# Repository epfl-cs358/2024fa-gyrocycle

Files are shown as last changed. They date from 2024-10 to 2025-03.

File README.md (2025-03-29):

# GyroCycle

Welcome to the GyroCycle project's repo!

GyroCycle is a project of building a self-balancing bicycle as part of the [CS-358 course at EPFL](https://edu.epfl.ch/coursebook/en/making-intelligent-things-a-CS-358-A).

This is the result we came up with:

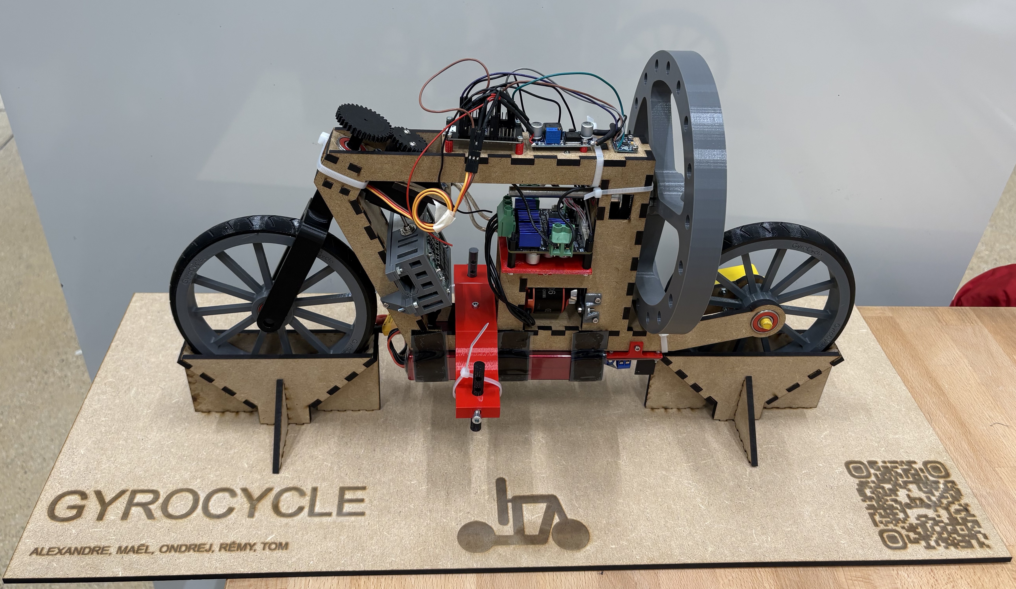
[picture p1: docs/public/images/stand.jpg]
The result bicycle on its stand.


We documented our results along with how to reproduce the build on our [documentation website](https://epfl-cs358.github.io/2024fa-gyrocycle/).

Happy building !

The GyroCycle team.

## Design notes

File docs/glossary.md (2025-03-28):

---
prev: false
next: false
---

<script setup>
    import StlViewer from "./.vitepress/theme/components/StlViewer.vue";
</script>

# Glossary

Some particular words are used for specific meanings in the context of GyroCycle. Those meanings are described here.

## Child Wheels

In the context of GyroCycle, _child wheels_ refer to the safety part of the bike that prevents the bicycle from completely falling on its side. Instead, it stops the fall at a reasonable angle, hence its name.

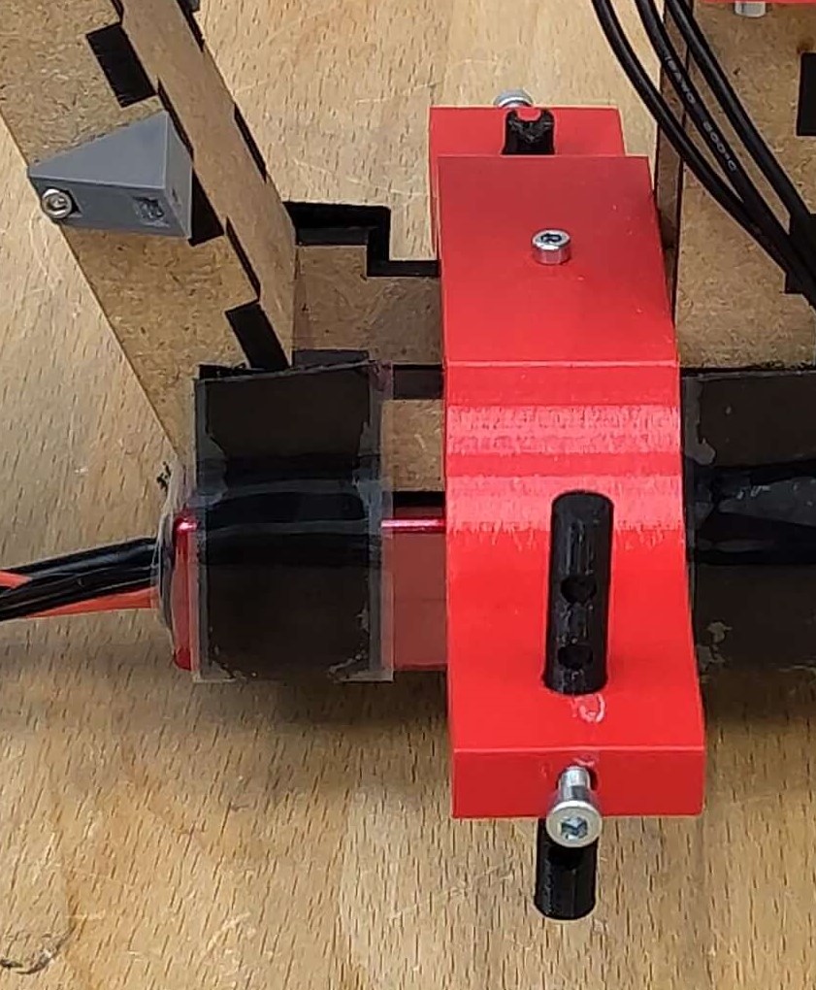
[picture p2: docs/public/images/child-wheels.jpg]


## Flywheel

GyroCycle uses a _flywheel_ to balance. A flywheel is a wheel that rotates to resist changes in motion and counter some other force, in our case the tilt of the bicycle.

When we say flywheel we refer to the big flywheel component at the back of the bicycle.

<StlViewer stlUrl="/2024fa-gyrocycle/stl/to-be-printed/flywheel.stl" />

## Stand

In the context of GyroCycle, the stand is the support structure we built to hold the bicycle upright when it is not balancing, allowing us to showcase it.



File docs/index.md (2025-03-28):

---
title: GyroCycle Docs
prev: false
next: false
---

# GyroCycle

Welcome to our documentation website!

GyroCycle is a course project worked on as part of the [CS-358 course at EPFL](https://edu.epfl.ch/coursebook/en/making-intelligent-things-a-CS-358-A) by a group of five students.

This is the end product:

GyroCycle bicycle on its stand

## Features

The bicycle is designed to balance itself, meaning that when started, it will measure its tilt angle, and rotate the gray flywheel accordingly to compensate for the tilt and stay upright.

One can also connect to the bicycle from a mobile phone using [RemoteXY](https://remotexy.com/en/download/). This way, one can tell the bicycle to steer right and left, and to drive forward and backward.

## Try it

We provide detailed instructions and documents to build your own GyroCycle. See the [guide](./guide/) for more information.

## Video

Here you can see the bike in action (with the noise it makes...).

<video controls="controls" src="/videos/balancing-bicycle.mp4" style="max-height: 50vh;" />

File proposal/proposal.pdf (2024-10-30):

MiT Team Project - GyroCycle | 1

# GyroCycle – Self-balancing bicycle

CS-358 MAKING INTELLIGENT THINGS – TEAM PROJECT PROPOSAL

By Tom Vrakking, Ondrej Zedka, Rémy Berguerand, Maël Imhof and Alexandre Hetet

## Description

Main idea. Create a small scale bicycle that balances itself automatically using physics laws. The bicycle could stay balanced while idle (sationnary) and while moving (forward, backward, turning left or right).
Furthermore, the bicycle could be controlled through a software interface such as a web or mobile app, to make the project more interactive.

Extended idea. Once the main idea is implemented, computer vision could be introduced for the bicycle to drive itself given some instructions or goal.

The motivation behind this project is to play with the laws of physics and build something cool and fun that can be used as a demo for future EPFL students, physics students, …

## Milestone 1 - Gyroscopic Balancing

The first stage focuses on the ability for the bike to balance on its own while stationary or while moving/turning. The stage is divided in three sub-stages

1. Balance when stationary
2. Make the bicycle able to move (forward, backward, turn left and right)
3. Balance while moving

## Stationary balancing

The team will first focus on building the bicycle itself and making sure it is able to automatically balance while stationary.
An accelerometer and gyroscope will be used to measure the bike’s tilt. The microcontroller will then adjust by accelerating the flywheel in the right direction to correct any imbalances.
Field-Oriented Control (FOC) will be used to control the wheel’s motor with the required precision. In addition to the main microcontroller, a FOC driver will thus be needed.
At this stage, the bicycle should already be designed in such a way that adding components for computer vision later does not require a complete redesign.

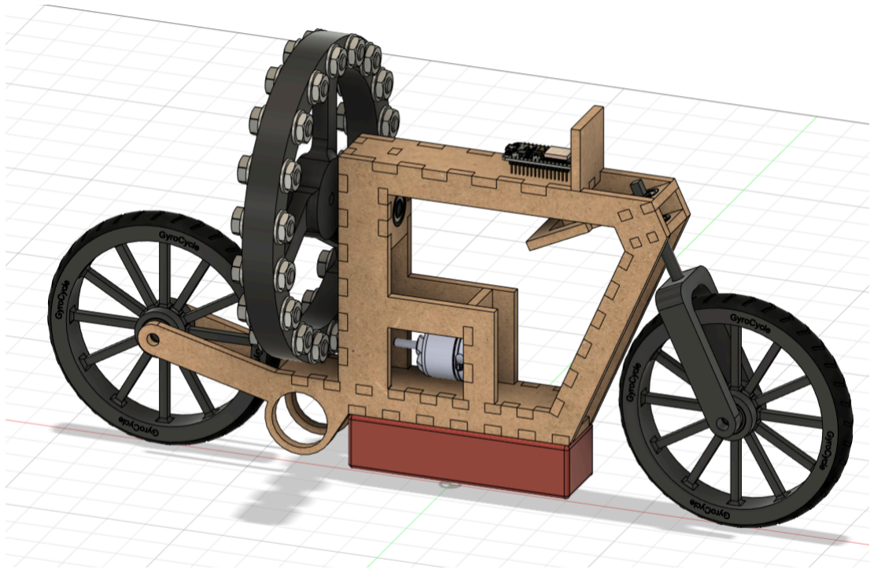
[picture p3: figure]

Mechanical build for stationary balancing. Note that motors for propulsion or steering are not in there yet.

Hardware
- Design and build the bike with computer vision in mind already
- Assemble and mount the electronics
- Make the bike look as pretty as possible
Software
- Implement stationary balancing

## Moving bicycle

Once the bicycle is able to stay balanced while stationary, the team will move on to making it able to move while still balancing itself.
This will require an additional motor for propulsion along with a servo motor for turning left and right.
The software will need to be updated to account for possible movement of the bicycle and to know how to balance it while either stationary or moving.

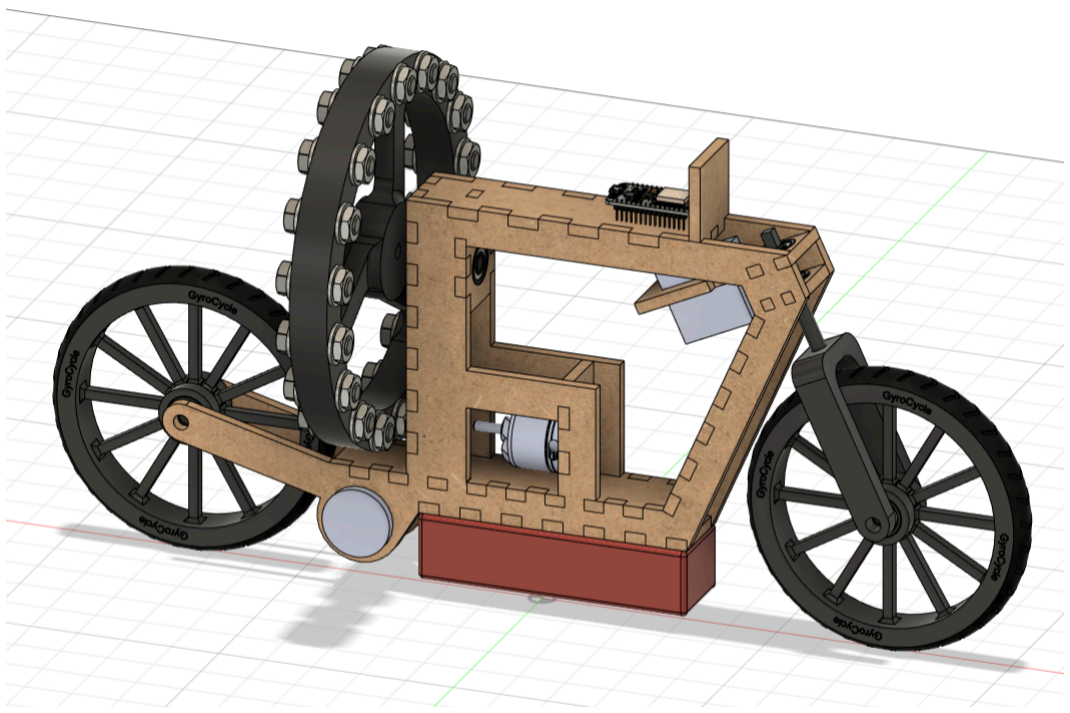
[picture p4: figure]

Moving bike. A propulsion motor is added at the bottom of the flying wheel and a steering servo is added on the front wheel’s axis.

Hardware
- Mount the propulsion motor and the servo
- Mount and connect the WiFi chip
- Mount and connect the camera
- Make sure the wheels can rotate smoothly
Software
- Implement a web portal or mobile app to remote control the bicycle
- Implement client-side software to receive and execute remote instructions

## Moving balanced bicycle

The bicycle is balanced at rest and can move as well, it should also be able to automatically balance while moving. This will be the next and final step of the first milestone for this project.
Ideally, software adaptations should suffice to make the bicycle balanced while moving. If needed (if something goes wrong, and something will probably go wrong), the hardware will need to be adapted as well.

Hardware
- Pray that nothing has to change
- Adapt the hardware if the software does not suffice

Software
- Implement balancing for the moving bicycle

## Milestone 2 - Computer Vision

The second stage of the project introduces computer vision for the bicycle to move automatically while avoiding obstacles.
If a camera was introduced on the hardware in milestone 1, it can be used, otherwise a camera will need to be mounted onto the existing assembly. Apart from this, changes to the physical assembly shouldn’t be necessary. The computer vision program should run on a laptop connected via WiFi and send commands just like the remote controller in milestone 1.
This milestone will hence be mostly software, since the main challenge will be to decide, based on a (relatively low-quality) video feed, which action to perform (turn left, turn right, …). The balancing will be handled by the bicycle itself and won’t require additional instructions from the laptop.

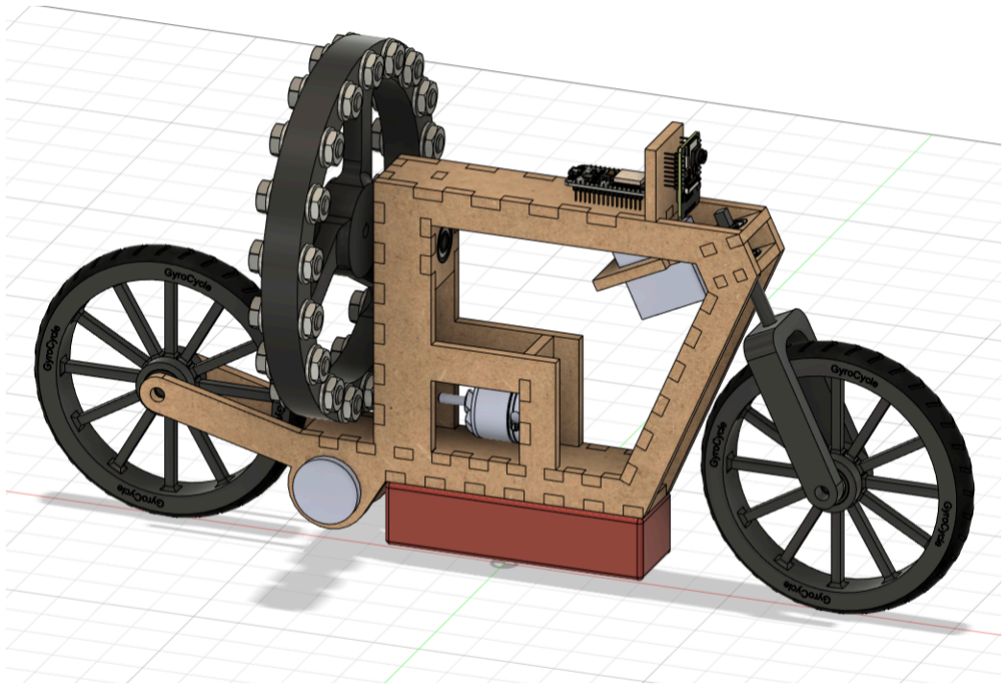
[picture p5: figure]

Addition of computer vision. Add an ESP32 camera at the front of the bike close to the other microcontroller.

Hardware
- Mount and connect the camera if not done before
Software

- Implement a computer vision algorithm that, based on the image sent by the camera and the current state of the bicycle, sends commands to the bicycle to avoid obstacles

## Optional improvements

Optionally, if there is time, the team will try to make computer vision work on the used microcontroller. As stated in the course manual :

Computer vision purely on an ESP32-CAM. It is possible, but so far in this course, teams have done the image processing on their laptops only.

Hence it would be an interesting challenge to tackle. It is however likely that time won’t allow this optional part to be done.

Hardware
- Add cooling or additional connections as needed for running computer vision on the microcontroller
Software
- Minimize, simplify and optimize the software for it to run on a microcontroller

## User Stories

The project represents an interesting demonstration of the laws of physics. and good entertainment for open doors at EPFL.
- As a physics teacher, I could use a self-balancing bicycle to demonstrate the laws of rotational physics to students in a very concrete way, as a project other students made.
- As an EPFL open doors event organizer, I could let people control the bicycle through its remote interface, to use it as an interactive demonstration of what is done at EPFL.
- As a high-school student, I would love seeing such a demonstration at EPFL open doors events, to show me how fun engineering can be and to motivate me to come to EPFL.

## Known and useful resources

A self-balancing bicycle, though an interesting project, is not a brand new idea. There are several resources out there that can help build such an idea.

A particularly helpful resource will be the YouTube channel of ReM-RC, (https://www.youtube.com/@ReMRC) dedicated to balancing things. Specifically, three videos are very similar to the present team project proposal:
- Self balancing bicycle (reaction wheel bike) (https://www.youtube.com/watch?v=UzjqdoTVhOU)
- DIY 3D printed self-balancing bike (https://www.youtube.com/watch?v=6snsCNyjHRU)
- Self balancing bike (https://www.youtube.com/watch?v=Je9Y2WaRB6g)
Those projects are open-source and available on GitHub. (https://github.com/remrc/Reaction-Wheel-Bike) They can already help in design and components decisions, and will later help implement software for balancing.

We will build a self-balancing bicycle using a flywheel and FOC to control said flywheel. An important resource for the project will be SimpleFOC, (https://simplefoc.com/#simplefoc_library) in particular their library and documentation.

At one point in the project, we will want the bicycle to move and to remotely control it from a mobile application. RemoteXY (https://remotexy.com/en/) can help by making it easy to implement such an app and connecting it to the hardware easily without reinventing the wheel (pun intended).

## Bill of materials

Category | Item (link) | Qty | Total Price (CHF)
MCU | NodeMCU ESP8266 V0.9¹ - Main microcontroller | 1 | 3.-
Power | 3S-11.1V, 5500 mAh, 20C (110A)¹ - LIPO battery | 1 | 52.-
| Lipo protection board¹ - LIPO protection circuit | 1 | 2.-
| XT90 male + female (https://www.bastelgarage.ch/xt90-connector-male-and-female) - LIPO connectors | 2 | 13.80
| Joy-it SBC-Buck01 (https://www.conrad.ch/fr/p/joy-it-sbc-buck01-regulateur-de-tension-1-pc-s-2582435.html) - Buck converter | 1 | 6.80
Balancing | MPU 6050¹ - Gyroscope + Accelerometer | 1 | 5.-
| Racerstar 3536¹ - Flywheel motor | 1 | 15.-
| AS5600¹ - Flywheel motor position sensor | 1 | 3.-
| STM32 B-G431B-ESC1¹ - FOC controller | 1 | 20.-
Moving | Motraxx SR545SA-4140P-67 (https://www.conrad.ch/fr/p/moteur-universel-a-balais-brushed-motraxx-sr545sa-4140p-67-1081972.html) - Propulsion motor | 1 | 11.95
| IBT-4¹ - Propulsion motor driver | 1 | 6.-
| DMS15¹ - Servo motor | 1 | 5.-
Computer vision | AIThinker ESP32-CAM w. Antenna¹ - Camera controller | 1 | 13.-
| FTDI USB-to-serial - Adapter for ESP32-CAM | 1 | 2.-
| TOF400H¹ - Laser distance sensors | 3 | 18.-
Miscellaneous | USB isolator¹ | 1 | 15.-
| Steel shaft 8mm x 500mm (https://www.conrad.ch/fr/p/arbre-en-acier-reely-o-x-l-8-mm-x-500-mm-237205.html?WT.srch=1) - Shaft for flywheel | 1 | 3.35
| Pack of 8 Bones Bearing Reds (https://www.galaxus.ch/fr/s4/product/bones-bearings-reds-roulement-a-billes-6424172?supplier=2403620) - ball bearings | 1 | 25.90
| GT2 Pulley 40 teeth 8mm Bore (https://www.3dware.ch/en/accessories/mechanics-accessories/3dware-ch-handelsware-01900944-40-gt2-pulley-40-teeth-8mm-bore) - For flywheel & wheel | 2 | 11.90
| GT2 Pulley 20 Teeth 6.35mm Bore (https://www.3dware.ch/en/accessories/mechanics-accessories/3dware-ch-handelsware-01900943-20-gt2-pulley-20-teeth-6-35mm-bore) - For flywheel motor | 1 | 4.20
| GT2 Pulley 20 Teeth 5mm Bore (https://www.3dware.ch/en/accessories/mechanics-accessories/3dware-ch-handelsware-01900907-20-gt2-pulley-20-teeth-5mm-bore) - For prop. motor | 1 | 3.-
| Shaft adapter 3.2mm to 5mm (https://www.galaxus.ch/fr/s5/product/hobbywing-adaptateur-pour-arbre-moteur-32-mm-a-5-mm-moteur-rc-18550175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) - For prop.motor/pulley | 1 | 5.50
| 1 meter of GT2 belt 6mm wide (https://www.3dware.ch/en/accessories/mechanics-accessories/3dware-ch-handelsware-01900906-6-gt2-pulley-6mm-wide) - Belts | 1 | 3.80

249.20

### 1. Parts in stock for CS358 (said in manual)

## Risk assessment, potential challenges

Such a project comes with challenges that will need to be addressed along the way. To prevent those challenges from impeding the success of the project, we list the ones we can think about below to plan in consequence.

- Working with LIPO batteries
The team has no experience with working with LIPO batteries. Those components bring additional security risks to the project, along with somewhat more complex powering of the components.
To mitigate risks relative to LIPO and to avoid damaging the circuit, rendering the project unusable, every team member is required to read the chapter 20 of the course manual and we will not hesitate to reach out to the course or DLL staff in case of any doubt or question.
Also, we will connect all electronic components together (including the LIPO) without mounting them on the bicycle first, to make sure the wiring is correct.
- Different power requirements
The project involves powering multiple sensors, actuators and microcontrollers that all have different power requirements. Managing power distribution and ensuring consistent supply without damaging components is crucial.
We will build an early prototype of the power system to double-check all components are powered correctly and function as expected, without mounting them on the bicycle yet.
- WiFi network stability
Giving remote instructions relies on using the WiFi of the ESP32 microcontroller to communicate between a phone and the bicycle. WiFi can be unstable or slow when used to give real-time instructions. This could affect the reactivity of the bike to user input, and later on to computer vision commands.
- Robustness
The bicycle will likely fall more than once when we test the balancing software. To prevent it from getting damaged, a team member should always be ready to manually catch the bike before it hits the ground.
- Computer vision and real-time video data
The second milestone introduces computer vision, which implies sending real-time video data from a microcontroller to an external laptop via WiFi, processing the real-time video data on the laptop as quickly as possible, and sending back commands to react to the situation.
The team will start by testing using only the ESP32 microcontroller and some simple obstacles to learn how to implement an algorithm that works on a low quality video flow.

## Organization

Milestone 1 (MS1) - self-balancing bicycle that can stand still or move, controlled through a web-app/mobile app

Idle but balanced Milestone B | Construct a downscaled bicycle that balances itself at rest
B1.1 Mechanical | ● Design and build a self-balancing bicycle with movement in mind already ● Document the hardware development in detail
B1.2 Balance software | ● Implement software to keep the bicycle balanced when idle ● Test the software and check the balance
Moving and balanced Milestone M | Add the capacity to move the bicycle through a web/mobile interface
M1.1 Adapted design | ● Add missing hardware for movement (motors for the wheels, motor for turning left and right) ● Document the hardware development in detail
M1.2 Control app | ● Implement a web/mobile app to control the bicycle through a WiFi connection.
M1.3 Controllable bicycle | ● Implement code for the microcontroller that will receive WiFi instructions from the app ● Marry the app and the hardware ● Adapt the balancing software to account for movement

Milestone 2 (MS2) - integrate computer vision so that the bicycle can automatically move and avoid obstacles

External computer vision Milestone E | Add a camera to the bicycle along with real-time processing with computer vision algorithms for the bicycle to drive itself
E1.1 Adapted design | ● Add a camera to the bicycle both in the design and on the actual physical design ● Document the hardware development in detail
E1.2 Computer vision software | ● Implement software to process the feed of the camera and output instructions to the bicycle
E1.3 Self-driving bicycle | ● Marry the adapted design with the camera and the computer vision software ● The computer vision software should run on a separate laptop for now
Mounted computer vision Milestone O | O for Optional. If there is time, adapt the computer vision software so that it can run directly on the microcontroller
O1.1 Adapted software | ● Adapt the computer vision software (scale it down, optimize it) so that it can run on the microcontroller

## Detailed Plan

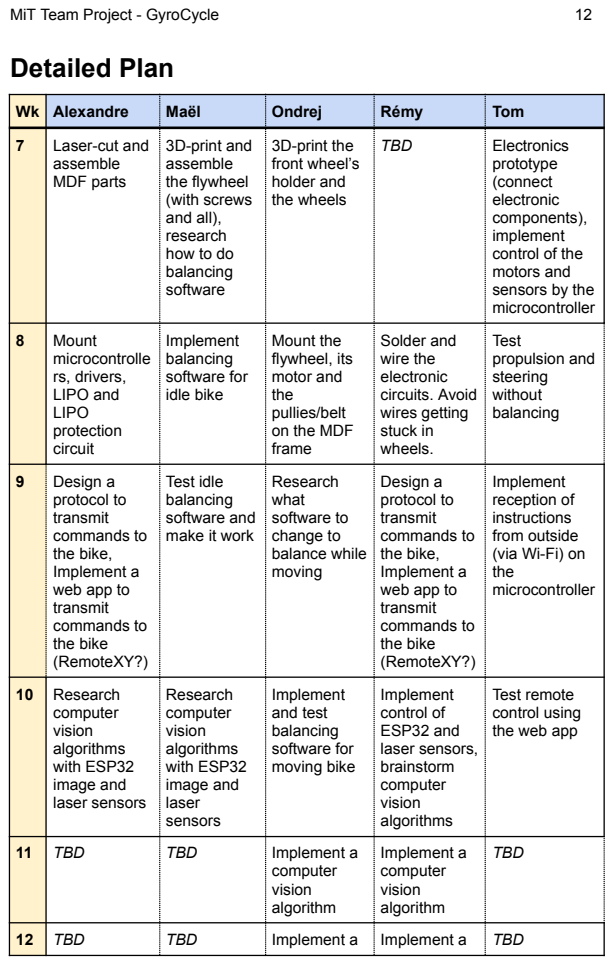
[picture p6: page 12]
8 Mount microcontrolle rs, drivers, LIPO and LIPO protection circuit; Implement balancing software for idle bike; Solder and wire the electronic circuits. Avoid wires getting stuck in wheels.; Test propulsion and steering without balancing; 9 Design a protocol to transmit commands to the bike, Implement a web app to transmit commands to the bike (RemoteXY?); Design a protocol to transmit commands to the bike, Implement a web app to transmit commands to the bike (RemoteXY?)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

Wk | Alexandre Maël Ondrej Rémy Tom

7 Laser-cut and | 3D-print and 3D-print the TBD Electronics assemble assemble front wheel’s prototype MDF parts the flywheel holder and (connect (with screws the wheels electronic and all), components), research implement how to do control of the balancing motors and software sensors by the microcontroller

Mount the
flywheel, its
motor and
the
pullies/belt
on the MDF
frame
Research
what
software to
change to
balance while
moving

Test idle
balancing
software and
make it work

Implement
reception of
instructions
from outside
(via Wi-Fi) on
microcontroller

Test remote
control using
the web app

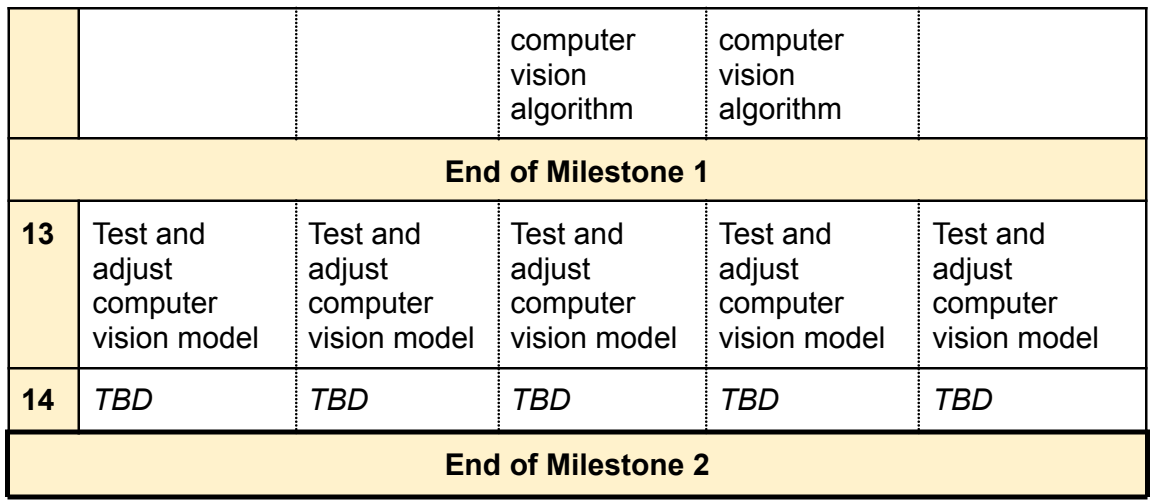
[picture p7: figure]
computer vision algorithm; End of Milestone 1; TBD TBD TBD TBD TBD; End of Milestone 2

Planning ahead is a difficult task, especially for projects in domains you do not know that well. The above is an optimistic plan that tries to account for problems by introducing TBD slots where the people are not assigned to anything in particular for now.
The tasks will be assigned during the SCRUM meetings anyway, this planning is only a tentative list of steps to reach the objective of the project.
Also, the planning highly depends on when the needed material will be delivered by suppliers. If hardware comes earlier or later than anticipated, the plan could drastically change.
13 Test and | Test and Test and Test and Test and adjust adjust adjust adjust adjust computer computer computer computer computer vision model vision model vision model vision model vision model

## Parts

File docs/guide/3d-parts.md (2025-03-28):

<script setup>
    import ComponentsToPrintTable from "../.vitepress/theme/components/ComponentsToPrintTable.vue";
</script>

# 3D-Printed Parts

Some parts of the bike need to be 3D-printed. All parts are to be printed in [**PETG**](https://en.wikipedia.org/wiki/Polyethylene_terephthalate), except the bike's tires that are to be printed in [**TPU**](https://en.wikipedia.org/wiki/Thermoplastic_polyurethane) for better elasticity.

Below is a list of `.stl` files to be 3D-printed, along with how many of each must be printed and in what material.

::: tip
You can download all of the `.stl` files as a single `.zip` with <a href="/2024fa-gyrocycle/zip/gyrocycle-parts-to-3d-print.zip" download>this link</a>.
:::

<ComponentsToPrintTable />

Once all 3D parts have been printed, the power supply circuitry of the bicycle needs to be soldered together, which is detailed in the next section.

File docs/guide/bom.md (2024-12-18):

# Bill of Materials (BoM)

In addition to tools, 3D-printed parts and laser-cut parts, you will need generic pieces and electronical components to build the bike. Here is a list ([BoM](https://en.wikipedia.org/wiki/Bill_of_materials)) of the required components for GyroCycle:

<table>
    <thead>
        <tr>
            <th>Category</th>
            <th>Description</th>
            <th>Reference</th>
            <th>Qty</th>
        </tr>
    </thead>
    <tbody>
        <tr>
            <td>MCU</td>
            <td>Main microcontroller</td>
            <td>NodeMCU ESP32</td>
            <td>1</td>
        </tr>
        <tr>
            <td rowspan="6">Power</td>
            <td>LIPO battery</td>
            <td>3S-11.1V, 5500 mAh, 20C (110A)</td>
            <td>1</td>
        </tr>
        <tr>
            <td>LIPO protection circuit</td>
            <td>BMS 3S (12.6V – 60A) Lithium Battery Protection Module (Balanced)</td>
            <td>1</td>
        </tr>
        <tr>
            <td>Connector to plug the LIPO in</td>
            <td>XT90 male</td>
            <td>1</td>
        </tr>
        <tr>
            <td>Intermediate connectors for LIPO</td>
            <td>XT60 male + female pair</td>
            <td>2</td>
        </tr>
        <tr>
            <td>On-Off switch</td>
            <td>-</td>
            <td>1</td>
        </tr>
        <tr>
            <td>Buck converter</td>
            <td>Joy-it SBC-Buck01</td>
            <td>1</td>
        </tr>
        <tr>
            <td rowspan="8">Balancing</td>
            <td>Gyroscope and accelerometer</td>
            <td>MPU 6050</td>
            <td>1</td>
        </tr>
        <tr>
            <td>Flywheel motor</td>
            <td>Racerstar 3536</td>
            <td>1</td>
        </tr>
        <tr>
            <td>Flywheel motor optical position sensor</td>
            <td>AMT102-V</td>
            <td>1</td>
        </tr>
        <tr>
            <td>Flywheel motor FOC controller</td>
            <td>ODrive v3.6</td>
            <td>1</td>
        </tr>
        <tr>
            <td>Bearings for wheels</td>
            <td><a href="https://www.galaxus.ch/fr/s4/product/bones-bearings-reds-roulement-a-billes-6424172?supplier=2403620">Pack of 8 Bones Bearing Reds</a></td>
            <td>1x8</td>
        </tr>
        <tr>
            <td>Flywheel pulley</td>
            <td>GT2 Pulley 40 teeth 8mm Bore</td>
            <td>1</td>
        </tr>
        <tr>
            <td>Flywheel motor pulley</td>
            <td>GT2 Pulley 20 Teeth 6.35mm Bore</td>
            <td>1</td>
        </tr>
        <tr>
            <td>Belt between flywheel and motor</td>
            <td>GT2 belt 6mm wide 232mm long (we used <a href="https://www.3dware.ch/en/accessories/mechanics-accessories/3dware-ch-handelsware-01900920-232-gt2-belt-6mm-wide-232mm-long">this one</a>)</td>
            <td>1</td>
        </tr>
        <tr>
            <td rowspan="3">Moving</td>
            <td>Propulsion motor</td>
            <td>TT motor yellow geared</td>
            <td>1</td>
        </tr>
        <tr>
            <td>Propulsion motor driver</td>
            <td>L298N</td>
            <td>1</td>
        </tr>
        <tr>
            <td>Steering Servo</td>
            <td>DMS15</td>
            <td>1</td>
        </tr>
        <tr>
            <td rowspan="1">Miscellaneous</td>
            <td>USB isolator</td>
            <td>-</td>
            <td>1</td>
        </tr>
    </tbody>
</table>

A few notes about the above BoM.

- We do not provide a reference for the USB isolator, because no particular one should be needed. It is only a component meant to protect your laptop in case of back-EMF or problems with the LIPO, we recommend you use one.

- We do not provide a reference for the On-Off switch either because it shouldn't matter, just make sure it can whistand the voltage and current provided by the protection circuit to the bicycle components.

- In the original build, we had problems with the LIPO protection circuit (it prevented us from giving enough current to the motor), so we removed it (on course staff recommendation, and after talking to the SPOT staff). **[LIPOs are dangerous components](./words-of-caution), this was no trivial decision. Do not try this at home unless you know exactly what you are doing.**

- If you decide to go with no protection board (again, don't do this unless you know what you are doing), you could technically do without the XT60 connectors listed in the BoM, if you connect the LIPO directly to the power supply of the bicycle with a male XT90.

    We did not do this, as we had already soldered the XT60, and it would have taken more time to do with only one XT90 connector, but you might want to try this instead if you know what you are doing.

Now that the required equipment and components have been layed out, the next step is to start the actual manufacturing of the bike by meeting our CAD.

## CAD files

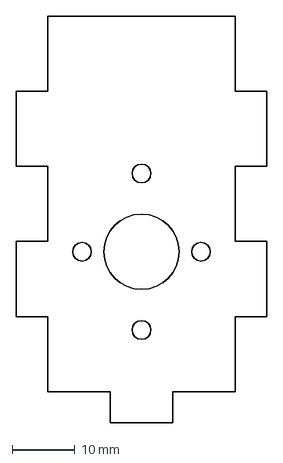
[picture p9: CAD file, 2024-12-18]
docs/public/dxf/bicycle-mdf-flywheel-motor-plate.dxf
40.0 x 65.0 mm

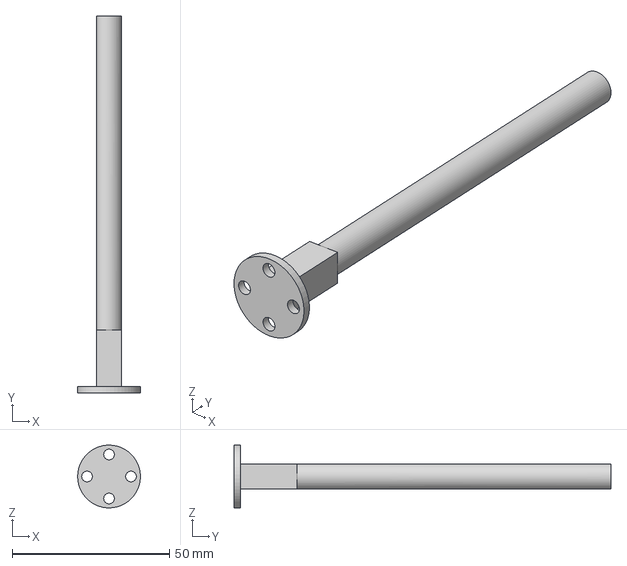
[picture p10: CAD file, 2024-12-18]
docs/public/step/flywheel-shaft.step
20.0 x 120.0 x 20.0 mm

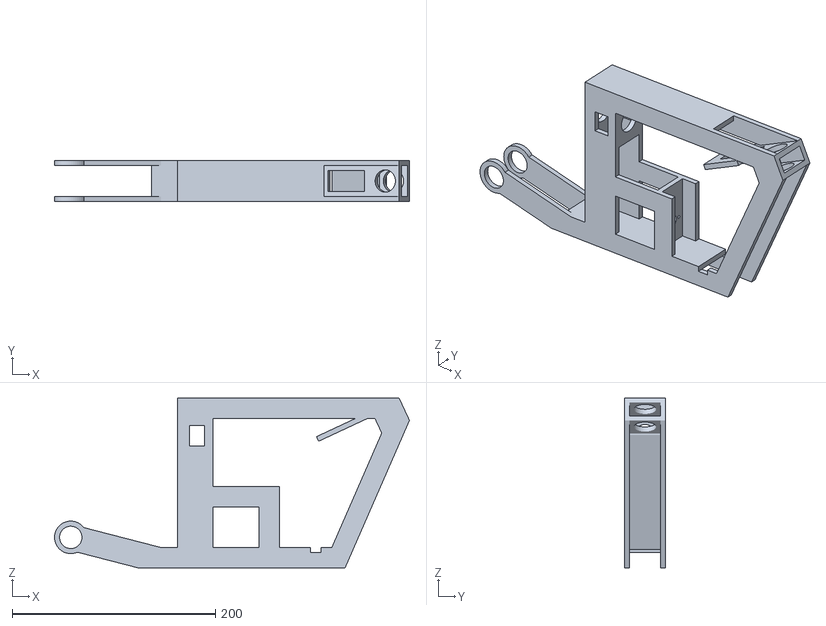
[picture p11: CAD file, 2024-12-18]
docs/public/stl/bicycle-mdf-frame.stl
348.9 x 40.0 x 166.9

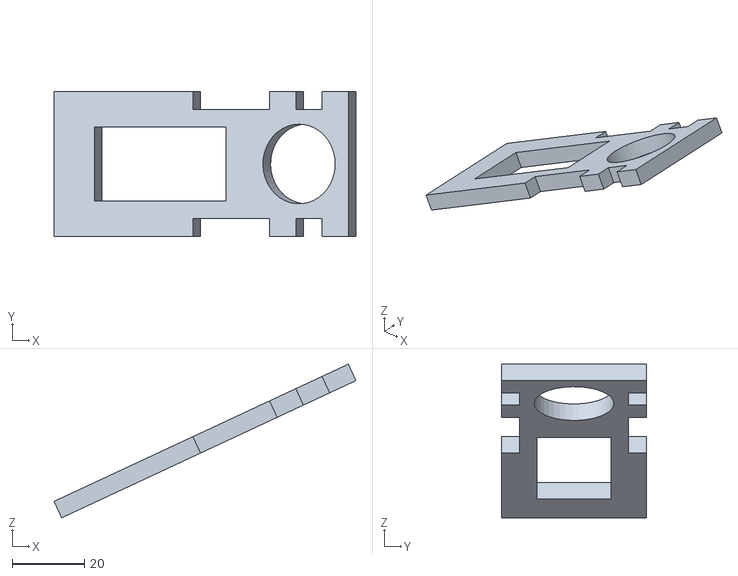
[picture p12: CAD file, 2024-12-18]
docs/public/stl/to-be-laser-cut/bicycle/bicycle-mdf-servo-holder.stl
83.3 x 40.0 x 42.4

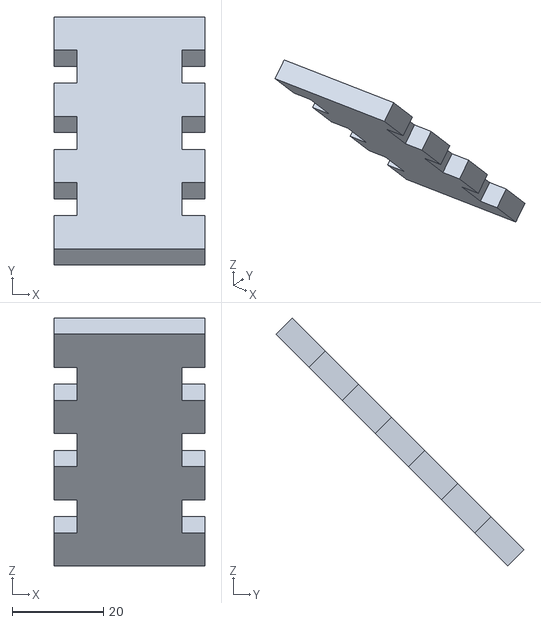
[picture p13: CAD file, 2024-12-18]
docs/public/stl/to-be-laser-cut/stand/stand-diagonal-side.stl
33.0 x 54.2 x 54.2

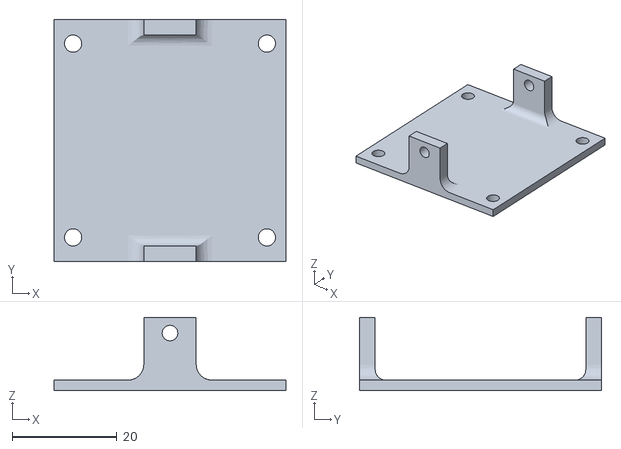
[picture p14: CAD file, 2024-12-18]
docs/public/stl/to-be-printed/propulsion-driver-plate.stl
44.3 x 46.2 x 14.0

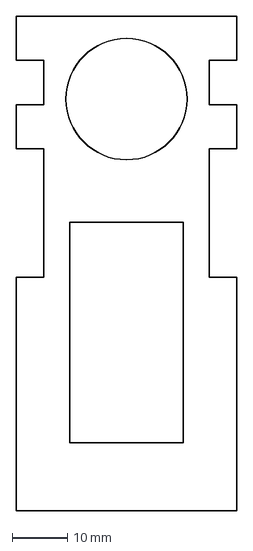
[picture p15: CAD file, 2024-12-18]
docs/public/dxf/bicycle-mdf-servo-holder.dxf
40.0 x 89.6 mm

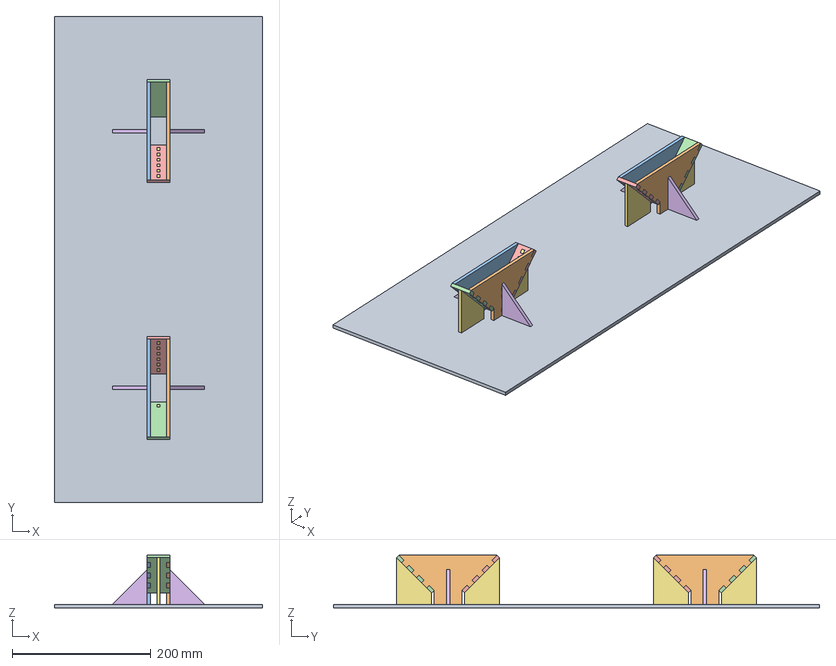
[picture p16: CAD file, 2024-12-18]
docs/public/step/stand-without-bicycle.step
300.0 x 700.0 x 75.7 mm

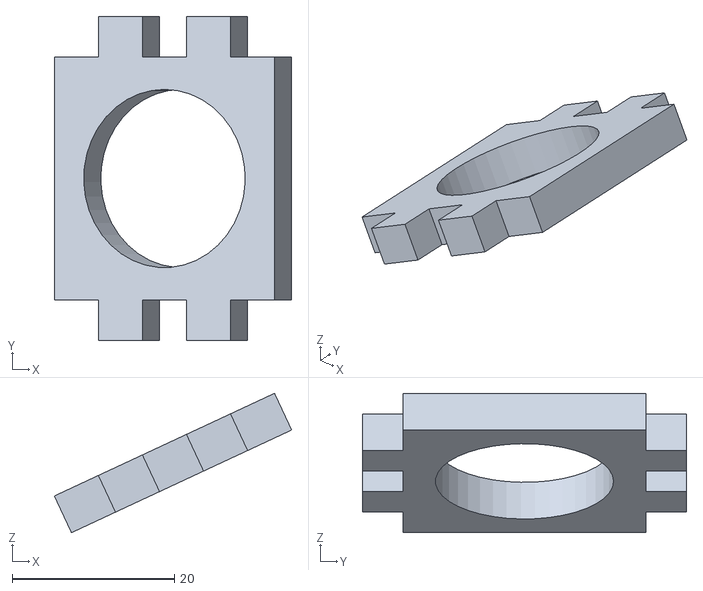
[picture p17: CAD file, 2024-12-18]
docs/public/stl/to-be-laser-cut/bicycle/bicycle-mdf-front-wheel-fork-holder.stl
29.3 x 40.0 x 17.2

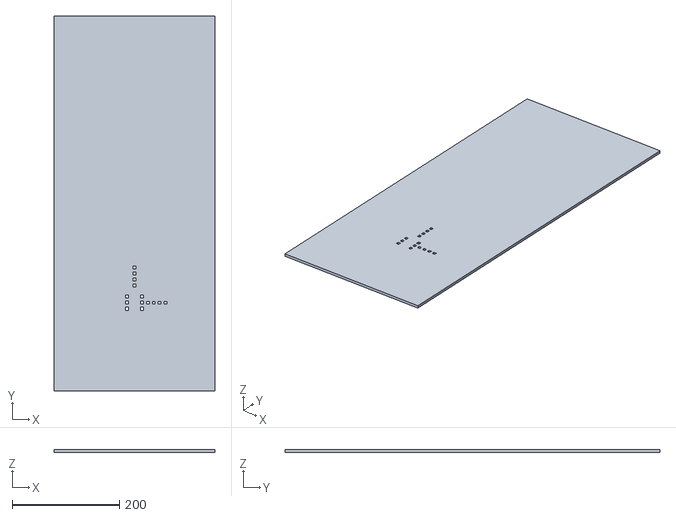
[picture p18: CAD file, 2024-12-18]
docs/public/stl/to-be-laser-cut/stand/stand-plate.stl
300.0 x 700.0 x 5.00

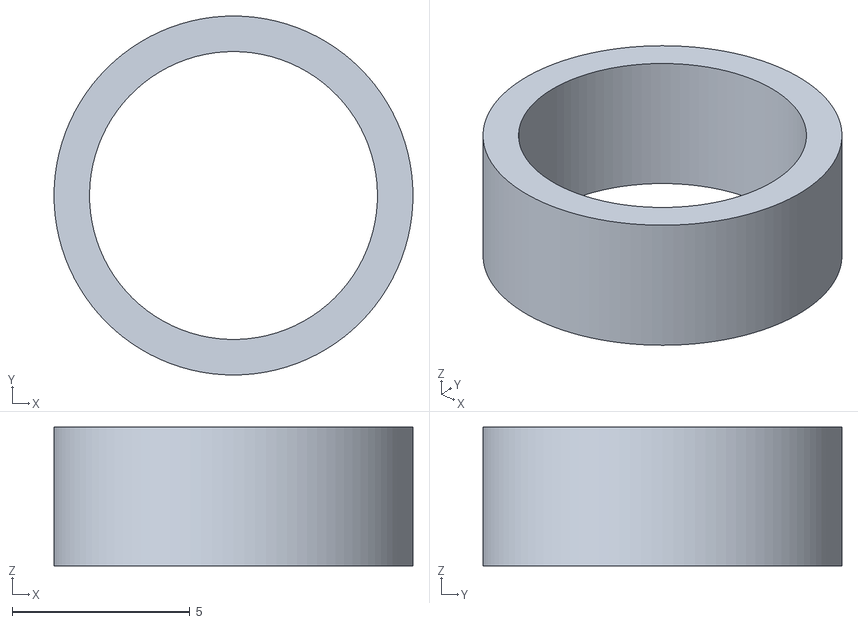
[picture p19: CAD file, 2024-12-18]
docs/public/stl/to-be-printed/front-wheel-spacer.stl
10.1 x 10.1 x 3.90

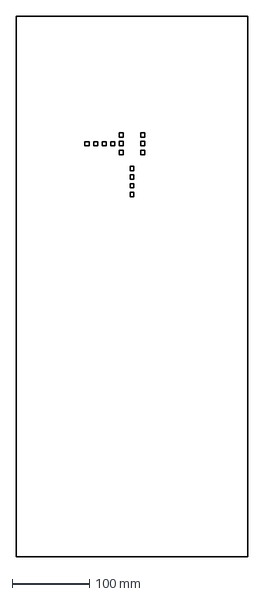
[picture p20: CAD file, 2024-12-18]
docs/public/dxf/stand-plate.dxf
300.0 x 700.0 mm

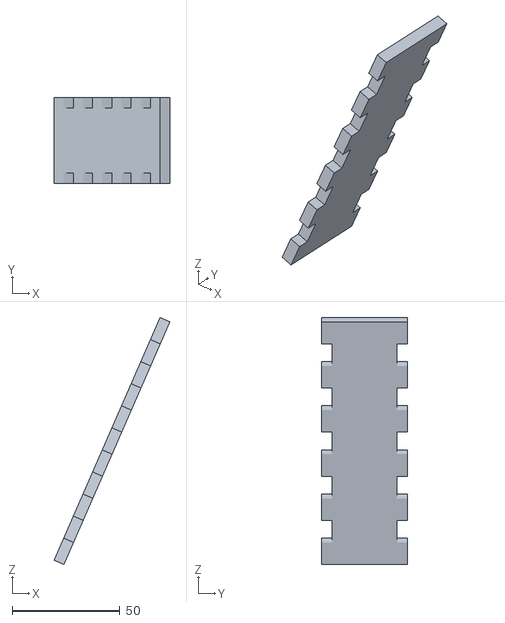
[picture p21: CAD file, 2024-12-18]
docs/public/stl/to-be-laser-cut/bicycle/bicycle-mdf-lipo-protection-circuit-support.stl
53.7 x 40.0 x 114.4

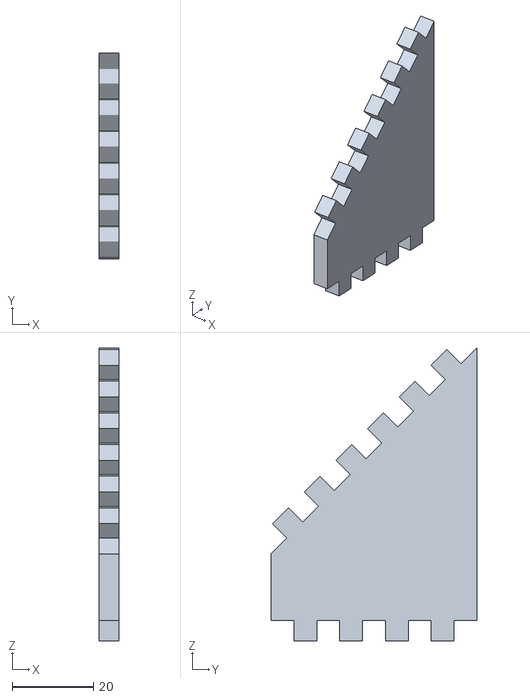
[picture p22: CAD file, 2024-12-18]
docs/public/stl/to-be-laser-cut/stand/stand-diagonal-support.stl
5.00 x 50.7 x 72.2

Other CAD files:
docs/public/stl/to-be-printed/rear-wheel-shaft.stl
docs/public/dxf/bicycle-mdf-lipo-protection-circuit-support.dxf
docs/public/stl/to-be-laser-cut/bicycle/bicycle-mdf-flywheel-holder.stl
docs/public/stl/to-be-laser-cut/stand/stand-vertical-side.stl
docs/public/dxf/bicycle-mdf-bottom.dxf
docs/public/dxf/bicycle-mdf-flywheel-holder.dxf
docs/public/dxf/bicycle-mdf-front-wheel-fork-holder.dxf
docs/public/dxf/bicycle-mdf-shaft-holder.dxf
docs/public/dxf/bicycle-mdf-side.dxf
docs/public/dxf/bicycle-mdf-top.dxf
docs/public/dxf/stand-diagonal-side.dxf
docs/public/dxf/stand-diagonal-support.dxf
docs/public/dxf/stand-vertical-side.dxf
docs/public/dxf/stand-vertical-support.dxf
docs/public/stl/flywheel-shaft.stl
docs/public/stl/stand-without-bicycle.stl
docs/public/stl/to-be-laser-cut/bicycle/bicycle-mdf-bottom.stl
docs/public/stl/to-be-laser-cut/bicycle/bicycle-mdf-flywheel-motor-plate.stl
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

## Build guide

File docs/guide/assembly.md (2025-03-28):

# Assembly

Once you have obtained the [required components](./bom), printed the [3D parts](./3d-parts), soldered the [circuitry](./soldering) and laser-cut the [MDF parts](./laser-cutting), you are ready to assemble all those pieces together.

Refer to our CAD, our blueprints and our electrical schema to assemble and wire everything together.

| Description | Download link |
| --- | --- |
| CAD `.step` file | <a href="/2024fa-gyrocycle/step/complete-bicycle.step" download>Download</a> |
| Bicycle blueprints (`.pdf`) | <a href="/2024fa-gyrocycle/pdf/bicycle-blueprint.pdf" download>Download</a>  |
| Electrical Schema (`.pdf`) | <a href="/2024fa-gyrocycle/pdf/electrical-schema.pdf" download>Download</a>  |
| Electrical Schema (`.zip` Kicad project) | <a href="/2024fa-gyrocycle/zip/electrical-schema.zip" download>Download</a>  |

Just a few notice before you start:

- Make sure to keep the ODrive's micro-USB port accessible, as the next step includes configuring it with `odrivetool`.

- You might observe that the shafts for the front and rear wheels of the bike have a too small diameter to properly fit in the bearings without floating.

  We solved this problem by adding tape on the shafts. This allowed us to add a few millimeters of diameter without re-printing the parts.

Once you assembled your bike, congratulations, you have the hardware ready! To make it work properly, there's one more step you need to take, and that would be the software setup.

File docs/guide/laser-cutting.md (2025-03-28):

<script setup>
    import StlViewer from "../.vitepress/theme/components/StlViewer.vue";
    import BicyclePartsToLaserCutTable from "../.vitepress/theme/components/BicyclePartsToLaserCutTable.vue";
    import StandPartsToLaserCutTable from "../.vitepress/theme/components/StandPartsToLaserCutTable.vue";
</script>

# Laser-Cut Parts

The bike's rigid frame is made out of MDF `5mm`. You will need a laser cutter to manufacture those pieces in a precise way.

Files for laser-cutting MDF parts are provided. There are two things to point out, though:

- Some of the screw holes were not added to the CAD. Hence, you might have to **drill additional screw holes** yourself if they are not already laser-cut.

- You might want to add a hole in one of the MDF parts to **make the bottom pulley in front of the motor visible**. In our original design, one has to disassemble a significant part of the bicycle before one can even see the bottom pulley, which caused us some problems for debugging.

Following is the list of parts to be laser-cut in an MDF plate, divided into two parts:

1. Parts for the bicycle itself.
2. Parts for the bicycle's stand. Those are not necessary if you only want to build the bike.

::: tip
You can download all of the `.dxf` files as a single `.zip` with <a href="/2024fa-gyrocycle/zip/gyrocycle-parts-to-laser-cut.zip" download>this link</a>.
:::

## Bicycle Parts

MDF parts to be laser-cut for the bicycle itself form the rigid frame of the bicycle.

::: details Preview of the rigid frame
<StlViewer stlUrl="/2024fa-gyrocycle/stl/bicycle-mdf-frame.stl" meshColor="#a16207" />
:::

<BicyclePartsToLaserCutTable />

## Stand Parts

We designed a stand to put the bike on when it is not balancing. Those are the parts needed to manufacture it.

::: details Preview of the stand with the bike on
<StlViewer stlUrl="/2024fa-gyrocycle/stl/stand-with-bicycle.stl" meshColor="#a16207" />
:::

::: details Preview of the stand without the bike
<StlViewer stlUrl="/2024fa-gyrocycle/stl/stand-without-bicycle.stl" meshColor="#a16207" />
:::

<StandPartsToLaserCutTable />

Once you have 3D-printed necessary parts and laser-cut others, you still need to manufacture a central piece of the bicycle: the metal shaft for the flywheel. This is the subject of the next section.

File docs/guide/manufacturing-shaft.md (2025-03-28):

<script setup>
    import StlViewer from "../.vitepress/theme/components/StlViewer.vue";
</script>

# Manufacturing the Flywheel Shaft

The flywheel shaft is a central component of the bicycle. It is the axis the flywheel will rotate on. Thus, it needs to be solid and whistand the forces meant to counter the bike's tilt.

For those reasons, we did not 3D-print this shaft, but manufactured a steel shaft instead.

## Documents

| Document | Link |
| --- | --- |
| 3D Model as `.step` file | <a href="/2024fa-gyrocycle/step/flywheel-shaft.step" download="flywheel-shaft.step">Download</a> |
| Blueprint for dimensions | <a href="/2024fa-gyrocycle/pdf/flywheel-shaft-blueprint.pdf" download="flywheel-shaft-blueprint.pdf">Download</a> |

::: details 3D Model Preview
<StlViewer stlUrl="/2024fa-gyrocycle/stl/flywheel-shaft.stl" />
:::

## Tips

Don't be scared to reduce the length a little bit. As you can see on pictures, our shaft was a bit too long.

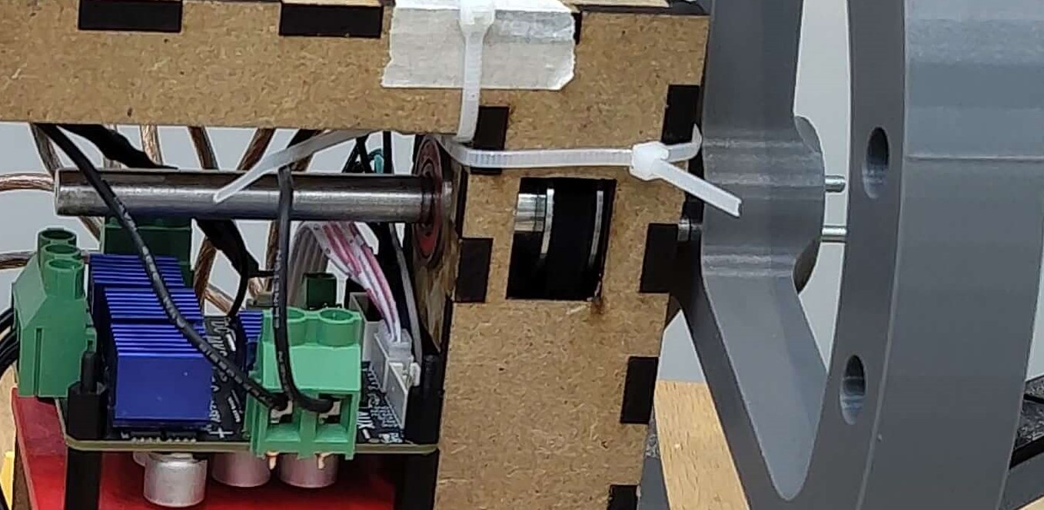
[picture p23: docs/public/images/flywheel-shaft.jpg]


::: tip
While manufacturing the steel shaft, make sure to stabilize it on both of its ends so that it does not bend during the process.
:::

The flywheel shaft was the last missing component. Now that all parts are available, we can start the actual assembly of the bike.

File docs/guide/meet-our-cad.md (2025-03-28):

<script setup>
    import StlViewer from "../.vitepress/theme/components/StlViewer.vue";
</script>

# Meet Our CAD

The bicycle was designed using the student trial of Fusion360. We provide both the CAD of the bicycle itself and the CAD of the stand we designed for the bicycle.

## Bicycle

You can download the complete bike CAD as a `.step` file from <a href="/2024fa-gyrocycle/step/complete-bicycle.step" download>this link</a>.

::: details Complete CAD Preview
<StlViewer stlUrl="/2024fa-gyrocycle/stl/complete-bicycle.stl" />
:::

There are two things we want to point out about this CAD.

1. If you look at the front wheel axle, at the top, you will see two gears used by the Servo to steer.

   The larger gear might seem too large because it overlaps on the smaller one. This is however expected. When 3D-printed, the two gears perfectly match.

2. The flywheel is linked to the motor with a belt and two pulleys. The top pulley is visible through a hole, but the bottom one is not.

   This is an improvement that we recommend you do when you laser-cut your own bicycle. Put a hole at the bottom of the bike where the flywheel motor is, so that you can see inside.

   We had several problems with the bottom pulley, and we always had to disassemble a good part of the bike to access it. Adding a hole would make this process much easier.

## Stand

We designed a stand to put the bike on when it is not balancing. You can download its CAD as a `.step` file from <a href="/2024fa-gyrocycle/step/stand-without-bicycle.step" download>this link</a>.

::: details Stand CAD Preview
<StlViewer stlUrl="/2024fa-gyrocycle/stl/stand-without-bicycle.stl" meshColor="#a16207" />
:::

Note that we added some text at the time of laser-cutting the MDF, to write the name of the project on the stand along with the QR code required to connect to RemoteXY (see the part about software).



## Electrical Schema

You'll find in the table thereafter links to download the electrical schema of GyroCycle, both in PDF format or for Kicad.

| Description | Download link |
| --- | --- |
| Electrical Schema (`.pdf`) | <a href="/2024fa-gyrocycle/pdf/electrical-schema.pdf" download>Download</a> |
| Electrical Schema (`.zip` Kicad project) | <a href="/2024fa-gyrocycle/zip/electrical-schema.zip" download>Download</a> |

Now that those have been pointed out, let's get into the manufacturing, starting with some soldering.

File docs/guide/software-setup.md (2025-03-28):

---
next:
  text: "You've done it!"
  link: "/guide/congrats"
---

# Software Setup

To balance itself, the bicycle needs software to be the orchestrator of the balancing and tell each component what it should do.

The NodeMCU ESP32 is the central component. It hosts and runs the software and is wired to other components to control them.

Following is a tutorial on how to setup the IDE, the software, along with other components to configure such as the ODrive and RemoteXY.

[[toc]]

## Setting up Arduino IDE

We used [Arduino IDE 2](https://docs.arduino.cc/software/ide/) for the software part of GyroCycle.

If you do not have it installed already, download and install the software on your machine from [this link](https://www.arduino.cc/en/software).

Because we used an ESP32 and not an Arduino, some additional steps are required, described below.

### Installing the ESP32 board

By default, Arduino IDE only supports Arduino devices. To compile and upload code for ESP32, you will have to add an `Additional boards manager`.

1. In Arduino IDE, go to `File` > `Preferences`

1. In the preferences window that opens up, at the bottom, there is an `Additional boards manager URL`. Paste the following URL into it:

   ```
   https://raw.githubusercontent.com/espressif/arduino-esp32/gh-pages/package_esp32_index.json
   ```

   If you already have other URLs, you can separate them with commas.

1. Go to `Tools` > `Board` > `Boards Manager...`

1. Search for `ESP32` and install the `esp32` by `Espressif Systems` version `3.X`

1. Wait for the installation to be done.

1. In the top drop-down device selector, you should see new boards appearing. Select `DOIT ESP32 DEVKIT V1` for GyroCycle.

::: tip FOR WINDOWS USERS
In addition to the above, Windows users need to download the `CP210x Windows VCP Driver` in order to detect the microcontroller. You can download it [here](https://www.silabs.com/developer-tools/usb-to-uart-bridge-vcp-drivers?tab=downloads).
:::

### Installing libraries

GyroCycle uses several libraries in its code.

| Library | Author | Version used | Comment |
| --- | --- | --- | --- |
| [`Adafruit MPU6050`](https://docs.arduino.cc/libraries/adafruit-mpu6050/) | Adafruit | `2.2.6` | For communication with the gyroscope sensor. **Installing this library will also install others that it depends on.** |
| [`ESP32Servo`](https://docs.arduino.cc/libraries/esp32servo/) | Kevin Harrington, John K. Bennett | `3.0.6` | To communicate with the Servo from the ESP32. |
| [`ODriveArduino`](https://docs.arduino.cc/libraries/odrivearduino/) | ODrive Robotics Inc. | `0.10.1` | To communicate with the ODrive from the ESP32. Even though we do not use an Arduino, the library contains useful functions and constants. |
| [`RemoteXY`](https://docs.arduino.cc/libraries/remotexy/) | Evgeny Shemanuev, RemoteXY | `3.1.14` | We use [RemoteXY](https://remotexy.com/) to remotelly control the bicycle from a phone. |

## Configuring the ODrive

GyroCycle uses an ODrive motor driver for its flywheel. That driver can be extensively configured. For example, you can provide it with a maximum speed for safety.

Configuring the ODrive is performed through the [`odrivetool`](https://docs.odriverobotics.com/v/0.5.6/getting-started.html#start-odrivetool) CLI.

::: warning
When wiring your ODrive to your computer, don't forget to use the USB isolator.
:::

### Installing `odrivetool`

1. Make sure [`matplotlib`](https://matplotlib.org/) is installed

   ```
   pip install matplotlib
   ```

1. Install [`odrivetool`](https://docs.odriverobotics.com/v/0.5.6/getting-started.html#start-odrivetool)

   ```
   pip install --upgrade odrive
   ```

1. Make sure the libraries installed with `pip` are in your PATH (you should be able to run `odrivetool` as a command in your terminal once installed)

1. If you are a Windows user, you need to install an additional driver. Skip this step if you are not using Windows.

   1. Download the driver installer [here](https://github.com/pbatard/libwdi/wiki/Install#user-content-Latest_official_release) (`Latest official release` section).

   1. Make sure your ODrive device is connected to your PC via USB

   1. Run the installer

   1. In the installer, under `Options`, make sure `List All Devices` is checked

   1. Find the ODrive in the list. Select the `Native Interface`

   1. Aside of `WinUSB`, click on the bottom arrow until you reach `libusb`

   1. Click on `Replace Driver`

   1. Wait for the process to finish

   1. Unplug and replug your ODrive if `odrivetool` was already running

1. Open a terminal

   ::: tip
   If you are using Windows, open the terminal as an administrator.
   :::

1. Run `odrivetool`

1. After a while, it should print `Connected to ODrive ...`, meaning it has recongized the connected ODrive device

Now that you successfully installed `odrivetool`, you can use it to configure your ODrive as documented below.

### ODrive Configuration

We provide a Python script that you can run once `odrivetool` is installed and set up.

Clone the repository or download the configuration file and run it as a Python script. Wait for it to succeed.

```
git clone https://github.com/epfl-cs358/2024fa-gyrocycle.git gyrocycle
cd gyrocycle/code
python3 odrv_config.py
```

::: info
You might see some error messages when the ODrive is asked to reboot. This is expected, and you should see right below:

```
Reboot command failed - this is normal
```

:::

## Upload the code to the ESP32

You have everything set up and wired, it is now time to put software on this bicycle.

1. If not already done, clone the GitHub repository to get the code

   ```
   git clone https://github.com/epfl-cs358/2024fa-gyrocycle.git gyrocycle
   ```

1. In the repository, open the `/code/gyrocycle/gyrocycle.ino` file in Arduino IDE

1. Connect the ESP32 board to your PC

   ::: warning
   Don't forget the USB isolator.
   :::

1. Make sure to select `DOIT ESP32 DEVKIT V1` as board type in Arduino IDE

1. In the top left corner of Arduino IDE, click the right arrow button (`Upload`)

1. Wait for the compiling to be done, then for the uploading to be done

   ::: tip
   During the hours we spent uploading code to the bicycle, we noticed that some of our team members had to hold the reset button of the ESP32 pressed when the compiling stopped and the uploading started, for the microcontroller to be in download mode.

   We can't fully explain why, but it worked. If you have trouble uploading code to the ESP32, you might want to give that a try.
   :::

Once the upload is successful (no errors displayed in red in Arduino IDE's console), your microcontroller is ready to control the whole bicycle.

## Use the software

It is finally time to turn this bad boy on!

1. Start the bicycle with the On-Off switch

1. Plug your laptop to the ESP32 (don't forget the USB isolator)

Once plugged and started, you should see some data coming via serial.

```
MPU6050 found.
Configuring the sensor...
Sensor configured.
Accelerometer range set to: +-2G
Gyro range set to: +- 250 deg/s
Filter bandwidth set to: 260 Hz
[...]
Setup complete.
Starting in 3...
2...
1...
```

Once the `1...` has been printed, you have entered what we called the **configuration mode**. It is designed for you to be able to change many configuration options and values without re-compiling and re-uploading the code (helped us a lot while testing).

You can use the `help` command (send `help` via serial) to get a list of available commands with their description. The main ones are

- **`config`**

  Defines the parameters for the balancing algorithm. Defines all parameters at once (except the filter, see below) to easily reproduce a configuration across runs, restarts and re-flashes.

  See the in-code `help` command for the exact order of parameters.

- **`filter`**

  Set the filter used for reducing the noise in the angle measurement. Possible values are [`KALMAN`](https://en.wikipedia.org/wiki/Kalman_filter) and [`EURO`](https://github.com/casiez/OneEuroFilterArduino/).

- **`set`**

  Individually set the parameters instead of using `config`. See the in-code `help` command for the exact names of possible parameters.

Here are the parameters used by our balancing algorithm.

| Name | Description | Type | Startup value |
| --- | --- | --- | --- |
| `controller_mode`  | What mathematical shenanigans to use to determine what torque the flywheel needs to provide. Possible values are `PID` and `OG`. Note that most of the following values are only used with `PID`. | `String` | `PID` |
| `angle_correction` | The MPU6050 (the accelerometer) might be slighty tilted or the angle prediction algorithm might have a constant error in its result. This is a simple offset that gets subtracted from the computed current tilting angle of the bicycle before the value is used. | `float`  | `-0.01` |
| `angle_margin` | How much margin there is for the bike to consider itself balanced. For example, if set to `0.02`, then the bicycle will consider itself balanced between `-0.02` and `0.02` angles, even though it's not perfectly at angle `0`. | `float`  | `0.00` |
| `filter` | When estimating the current tilting angle of the bicycle, vibrations or other hardware shenanigans might introduce significant amounts of noise. We use a filter to reduce this noise, either a `KALMAN` filter or an `EURO` filter. Use the `filter` command to change this parameter. | `String` | `KALMAN` |
| `Kp` | The _Kp_ coefficient of our [PID controller](https://en.wikipedia.org/wiki/Proportional%E2%80%93integral%E2%80%93derivative_controller). | `float`  | `1.5` |
| `Ki` | The _Ki_ coefficient of our [PID controller](https://en.wikipedia.org/wiki/Proportional%E2%80%93integral%E2%80%93derivative_controller). | `float`  | `0.0000001` |
| `Kd` | The _Kd_ coefficient of our [PID controller](https://en.wikipedia.org/wiki/Proportional%E2%80%93integral%E2%80%93derivative_controller). | `float`  | `0.1` |
| `max_fw_torque` | Safety limit for the torque the motor will provide for the flywheel. This is enforced by the ODrive, not in our software. | `float`  | Depends on your ODrive configuration. |
| `odrive_max_speed` | Safety limit for the velocity the motor will provide for the flywheel. This is enforced by the ODrive, not in our software. | `float`  | Depends on your ODrive configuration. |
| `setpoint_delta` | Introduces a dynamic setpoint instead of a static one. In the context our PID, the setpoint is the angle at which the bike considers itself balanced, so ideally angle `0`. This setpoint delta allows you to tell the bicycle to oscillate instead of trying to reach `0`. For example, if set to `0.02`, once the bicycle reaches the setpoint of `0.02`, the setpoint will be dynamically changed to `-0.02`, so the bike will try to oscillate between those two points. | `float`  | `0.02` |

::: tip
You can start with the following configuration, it worked pretty well for us.

```
algo PID
filter KALMAN
config 2.5 0.022 0.09 1 80 0 0.0245 0
```

:::

## Set up RemoteXY

You can use your mobile phone as a basic remote controller for the bicycle. You'll have to download the [RemoteXY](https://remotexy.com/en/download/) app on your phone.

Once you installed the app, make sure your bicycle is on, open the app and scan the following QR code:



It will tell your app all it needs to know to communicate with the ESP32.

That's pretty much it for setting up RemoteXY. Use the `ON/OFF` switch to enable/disable balancing. If disabled, the bicycle will stay still, otherwise it will balance itself using the flywheel.

The other sliders are for the Servo and the propulsion motor. Use them to steer the bike and make it go forward/backward.

::: info
Because of technical difficulties, we could not test the balancing software while in motion, so be careful if you try it.

If you find a good configuration, please [let us know](https://github.com/epfl-cs358/2024fa-gyrocycle/issues/new) so we can try it for ourselves and add it to the documentation.
:::

You now have a fully working reproduction of what we did as a semester project!

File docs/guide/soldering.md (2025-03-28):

# Soldering

GyroCycle requires you to solder a few wires together to properly work. Below is a description of what cables need to be soldered where.

Diagrams are provided below for easier reference, but you can also directly look at the electrical schema. Be warned though, not all connections on the electrical schema need to be soldered.

| Description | Download link |
| --- | --- |
| Electrical Schema (`.pdf`) | <a href="/2024fa-gyrocycle/pdf/electrical-schema.pdf" download>Download</a> |
| Electrical Schema (`.zip` Kicad project) | <a href="/2024fa-gyrocycle/zip/electrical-schema.zip" download>Download</a> |

## Soldering to the MPU6050

You will need to solder five **female connectors** to the MPU6050 sensor. A length of approximately 10 centimeters is fine for those. The wires need to be connected to

- `VCC`
- `GND`
- `SCL`
- `SDA`
- `INT`

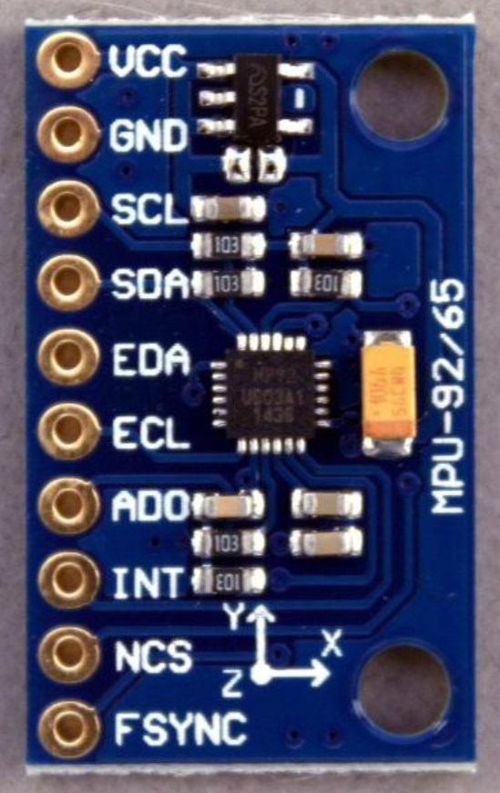
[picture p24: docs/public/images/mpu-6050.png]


## Soldering the LIPO protection circuit and power supply wires

To prepare the power-supply setup of the bicycle, refer to the schema below. Blue circles indicate where a solder is needed.

::: info
A part of the schema is dedicated to the On-Off switch of the circuit. We recommend you add one, however the way to solder it might defer depending on which one you got.
:::

::: warning
Make sure to use thick enough cables for the powered supplied from the battery and from the LIPO protection board.
:::

Make sure to also check the 3D printed pieces (next page of the guide) for the LIPO protection board. After soldering, printing and assembling, you should obtain something similar to the following:

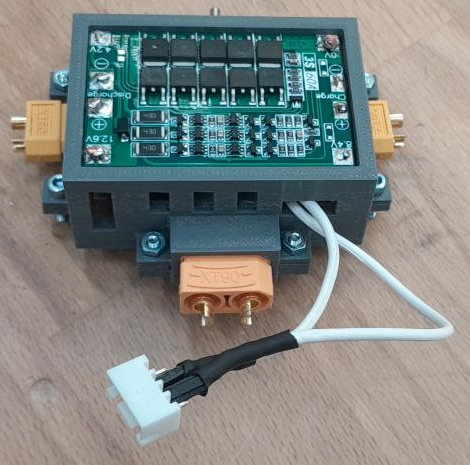
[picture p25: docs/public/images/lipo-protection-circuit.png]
Final result of the LIPO protection box


Plan the length of your cables accordingly.

Here is the diagram to help you with soldering:

Soldering schema for the LIPO protection board

Once all soldering has been done, we can move on to laser-cutting some parts.

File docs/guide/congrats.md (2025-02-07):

---
prev:
    text: Software Setup
    link: /guide/software-setup
next: false
---

# Congratulations !

You successfully built your own GyroCycle. Please share with us [on GitHub](https://github.com/epfl-cs358/2024fa-gyrocycle/issues/new) if you came that far, we would be glad to see your bicycle in action!

Thank you for reading this far.

Yours sincerely,

The GyroCycle team.

Alexandre, Maël, Ondrej, Rémy, Tom

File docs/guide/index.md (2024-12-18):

# Getting Started

Welcome to the DIY guide of the [GyroCycle](/) project. This guide is intended for you to build the bike for yourself, as GyroCycle is an [open-hardware](https://www.oshwa.org/definition/) project.

This guide will walk you through:

1. A few words of caution about the dangers of the project's components
1. The tools you will need access to
1. The necessary components (motors, microcontroller, ...)
1. How to manufacture the different parts of the bike
1. How to assemble the bike and wire everything together
1. How to upload and use the software

By following this guide, you should obtain a balancing bicycle.

Let's get right into it with a few words of caution.

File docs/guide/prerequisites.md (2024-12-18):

# Prerequisites

Unlink open-source software, open-hardware requires you to *build* the thing. Hence, you will need access to some tools to manufacture the bike:

- **3D Printer**
    
    Parts of the bicycle have to be 3D-printed. You will need access to a 3D-printer that can print with [**PETG**](https://en.wikipedia.org/wiki/Polyethylene_terephthalate) and [**TPU**](https://en.wikipedia.org/wiki/Thermoplastic_polyurethane) (for the bike's tires).

    We used a Prusa MK4 for the original build of GyroCycle, with a build volume of `250 x 210 x 220` millimeters.

- **Laser Cutter**

    The bike's rigid frame is made out of [MDF](https://en.wikipedia.org/wiki/Medium-density_fibreboard). Ideally, you will need a laser-cutter to manufacture its parts, as it needs to be quite precise.

    We used a BCL-0605MU laser cuter for the original build of GyroCycle, with a cutting area of `500 x 600` millimeters.

    ::: info
    We used another, bigger laser cuter for the stand of the bicycle, but the parts of the bicycle itself can be manufactured on a smaller area.
    :::

- **Soldering Equipment**

    The bicycle consists of several electronical components that need to be wired together. Most of the connections require cables to be [soldered](https://en.wikipedia.org/wiki/Soldering) together or to a board.

- **Milling Machine, Schaublin and Circular Sawivaan**

    Since the flywheel can go to great speeds and torques to control the bike's tilt, we manufactured the shaft it rotates on in steel using a few manufacturing machines.

    We used EPFL's [SPOT](https://www.epfl.ch/education/educational-initiatives/discovery-learning-program-2/prototyping/page-111858-en-html/) machines for the original build of GyroCycle. Specifically an [*Evolution Circular Sawivaan*](https://make.epfl.ch/equipment/113/evolution-circular-sawivaan), a [*Schaublin 102 Mi Cf Lathe*](https://make.epfl.ch/equipment/82/schaublin-102-mi-cf-lathe) and an [*Aciera F1 Milling Machine*](https://make.epfl.ch/equipment/84/aciera-f1-milling-machine).

- **Drill**

    Some screw holes might be missing from the CAD and the provided files to laser-cut. You will need to drill additional screw holes where needed.

In addition to those tools, you will need actual components and pieces to assemble the bicycle and make it work, move and balance. This is described in the next section, the Bill of Materials (BoM).

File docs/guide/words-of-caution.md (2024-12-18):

# A few Words of Caution

Before we go any further into the manufacturing and assembling of the bicycle, a few words of caution are advisable.

## Using a LIPO battery

Because the bicycle requires high currents to balance (the motor of the flywheel peaks to change direction and tilt the bike in the right direction), we use a LIPO battery for the project.

LIPO batteries are dangerous components. If not used right, they will likely explode in a fireball and/or release toxic chemicals. There are tons of YouTube videos that show this, for example [this one](https://www.youtube.com/watch?v=aZOKLpOn_W4).

If you want to build GyroCycle for yourself, make sure you know how to properly handle LIPO batteries, or that you know someone who does. As computer science students, we are unfortunately not qualified to write a complete guide on how to properly handle LIPO batteries.

## High-Speed Flywheel

The central balancing component of the bicycle is its flywheel. The role of the flywheel is to turn in a certain direction at a certain speed to counter the bicycle's tilting, thus making it stay stable.

To accomplish this role, the flywheel might start turning at very high speeds, which can be scary and dangerous if not solidly fixed.

Our strategy to mitigate this risk was to test the flywheel progressively. The motor driver we use provides a built-in maximum speed configuration. You should test your build with a small max speed at first. The bicycle might not balance very well with small speeds, but it will allow you to see whether your flywheel can withstand higher speeds.

## Disclaimer

We cannot provide any guarantee of the bicycle's safety. We built and tested it ourselves, however depending on how you build it you might encounter problems we do not know of.

Be careful, use common sense, and test step by step (for example, increase the flywheel's max speed progressively during the tests) to avoid injuring yourself or others.

With that in mind, let's dive into what you'll need to manufacture the bike.

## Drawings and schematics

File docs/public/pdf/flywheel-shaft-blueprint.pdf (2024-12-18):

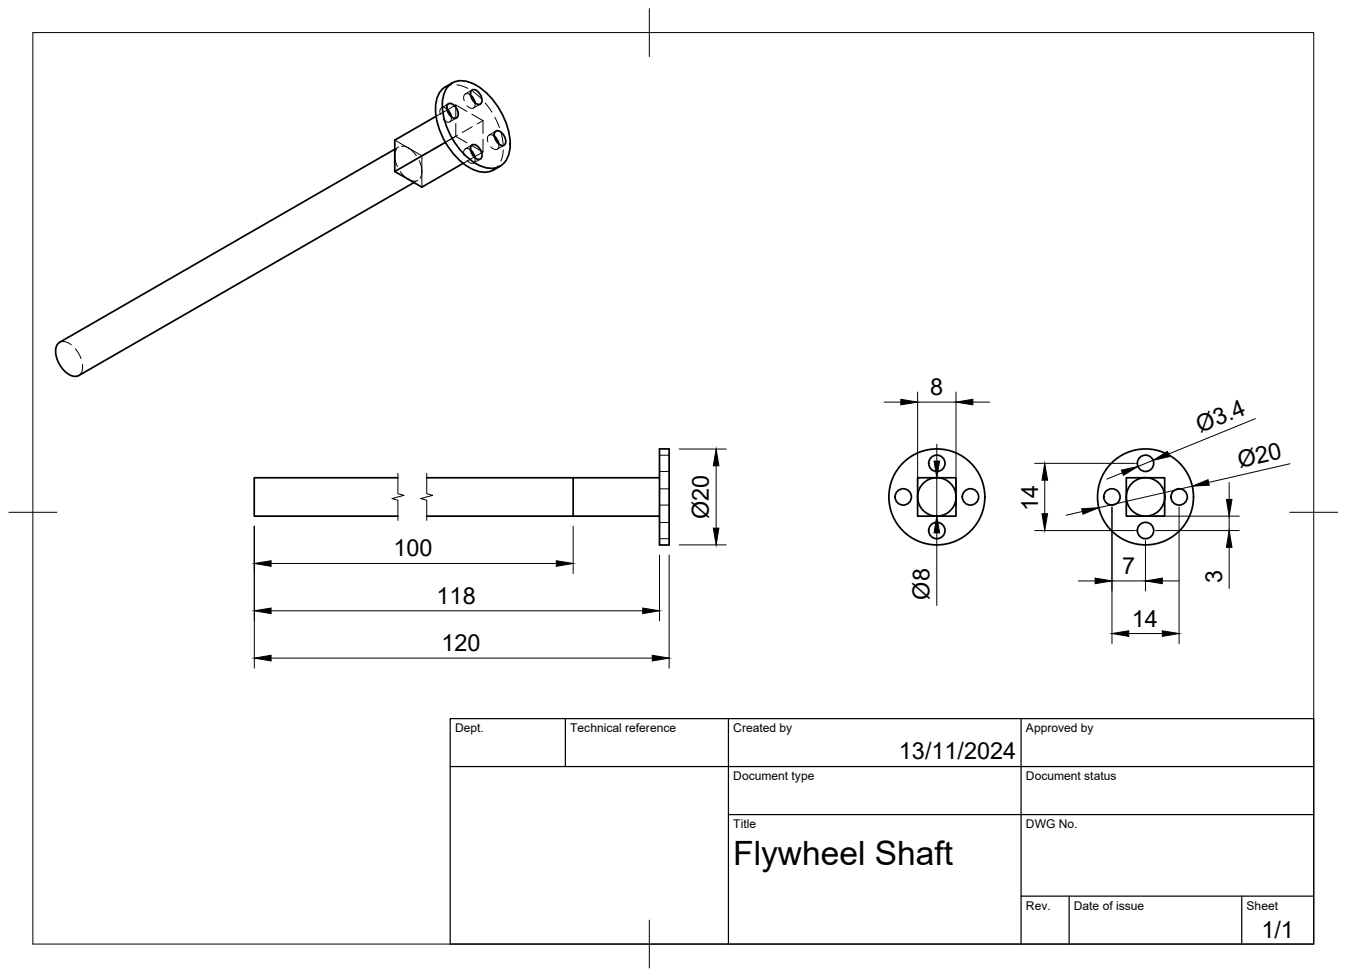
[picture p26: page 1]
Flywheel Shaft Ø20

Dept. | Technical reference | Created by 13/11/2024 | Approved by

Document type | Document status

Title | DWG No.

Rev. | Date of issue | Sheet 1/1

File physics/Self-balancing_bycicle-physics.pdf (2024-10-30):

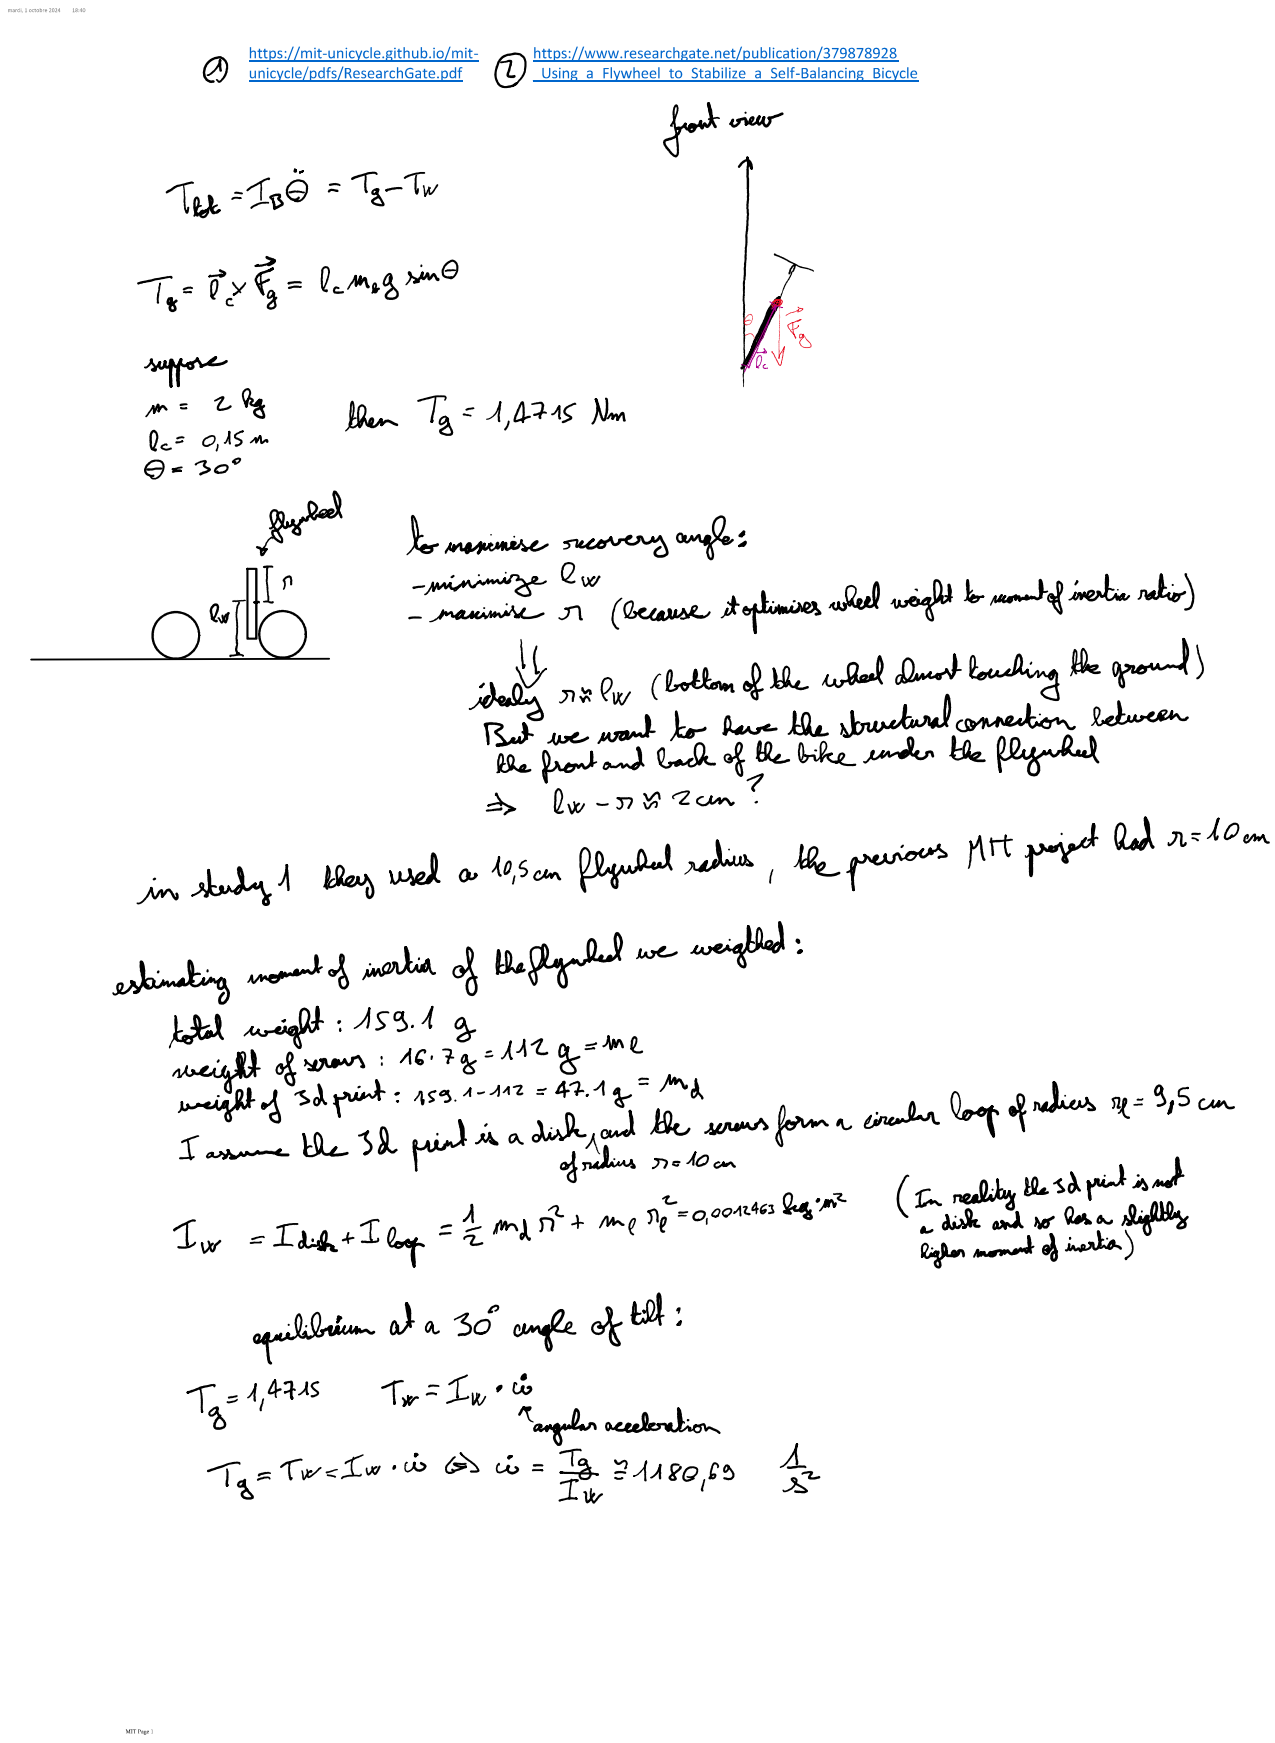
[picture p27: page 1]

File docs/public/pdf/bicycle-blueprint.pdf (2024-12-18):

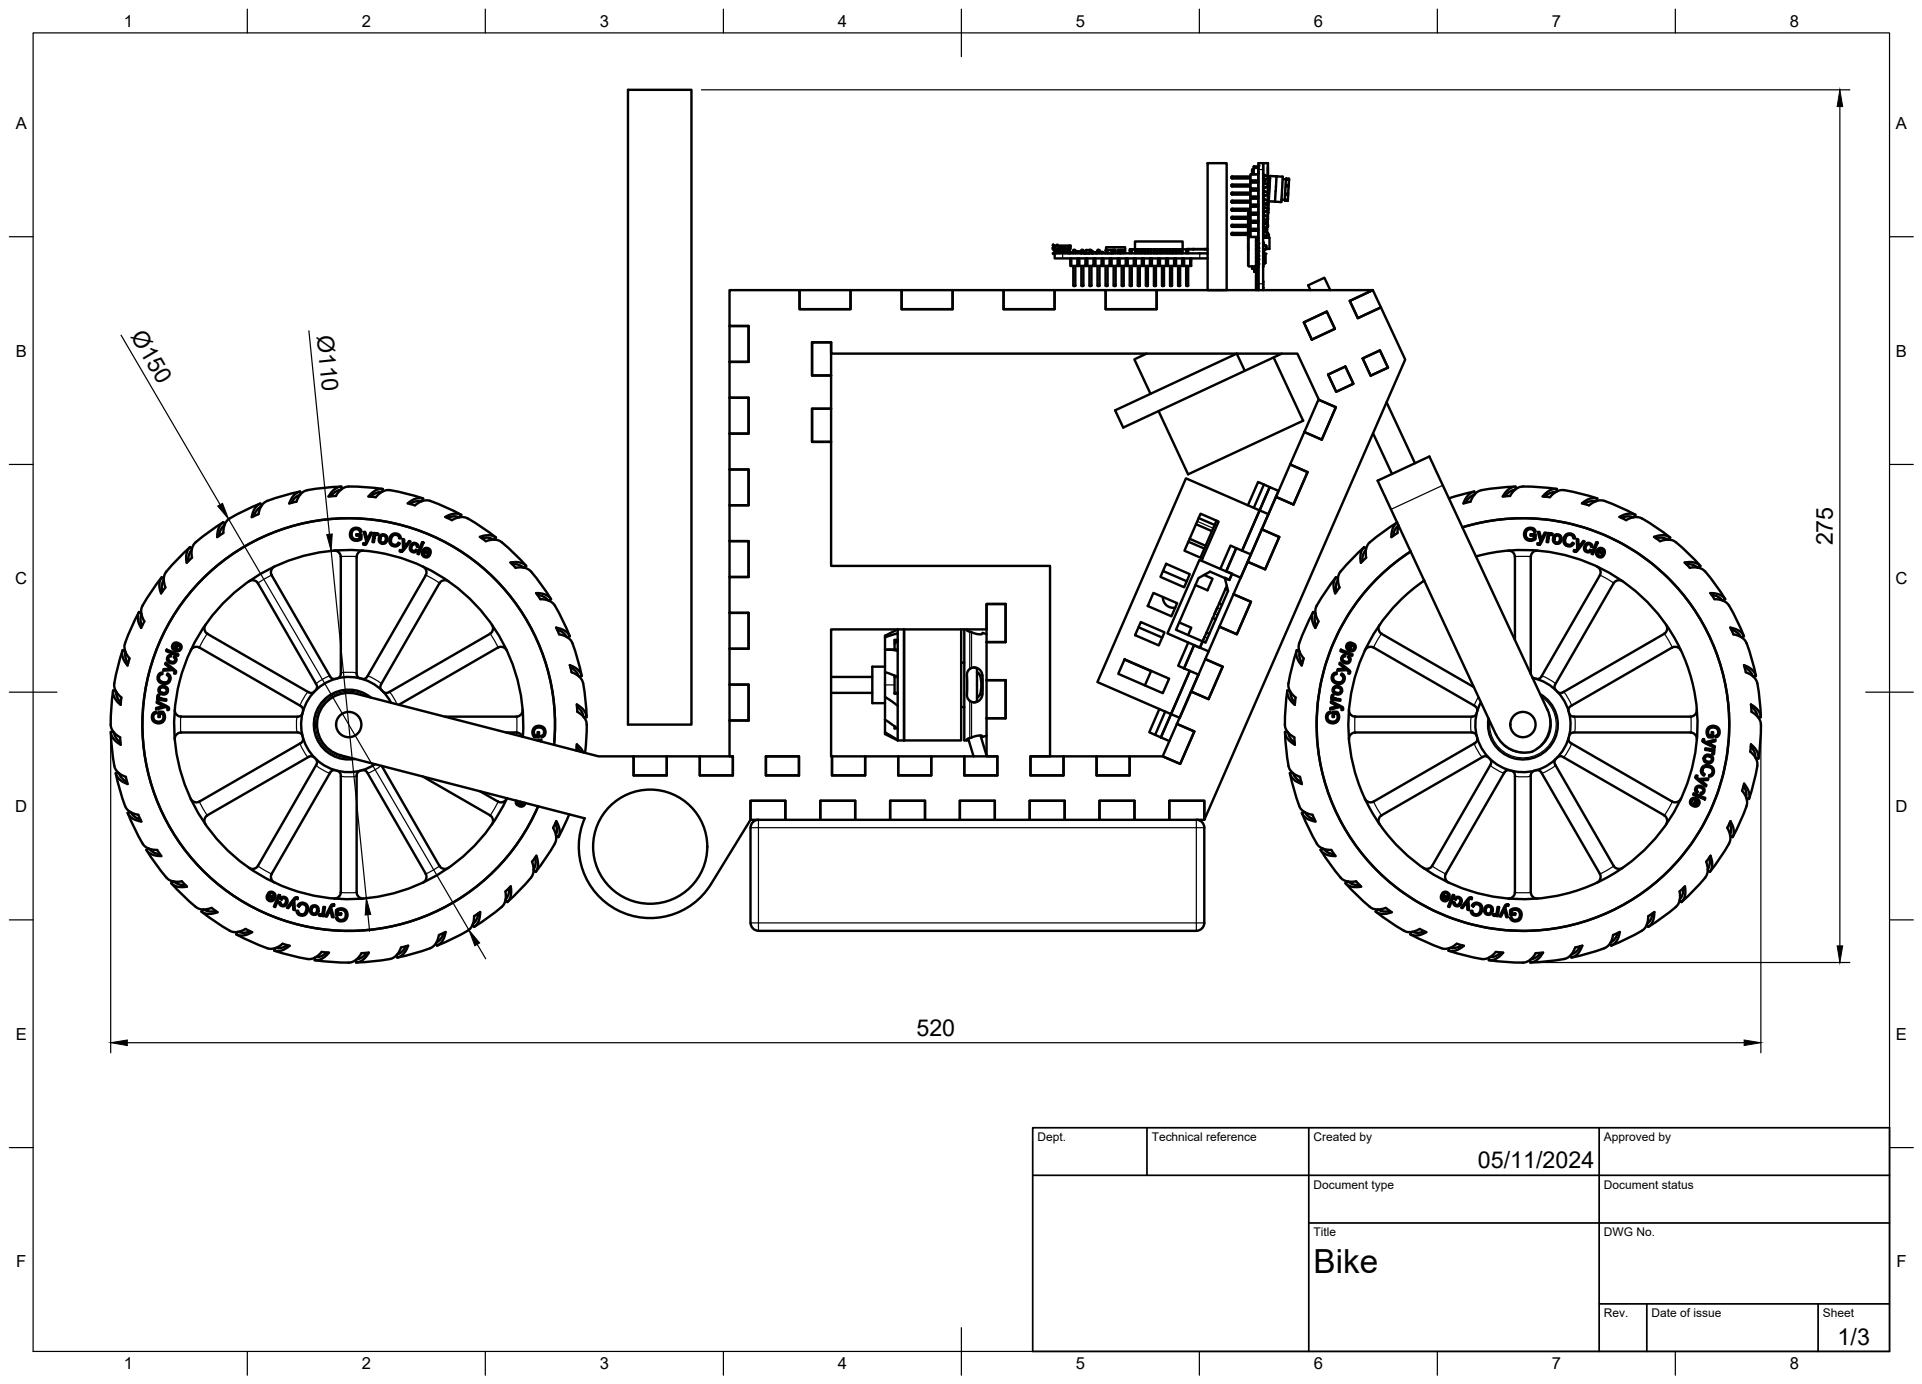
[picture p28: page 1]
Title; DWG No.; Rev.; Date of issue; Sheet

Dept. | Technical reference | Created by 05/11/2024 | Approved by

Document type | Document status

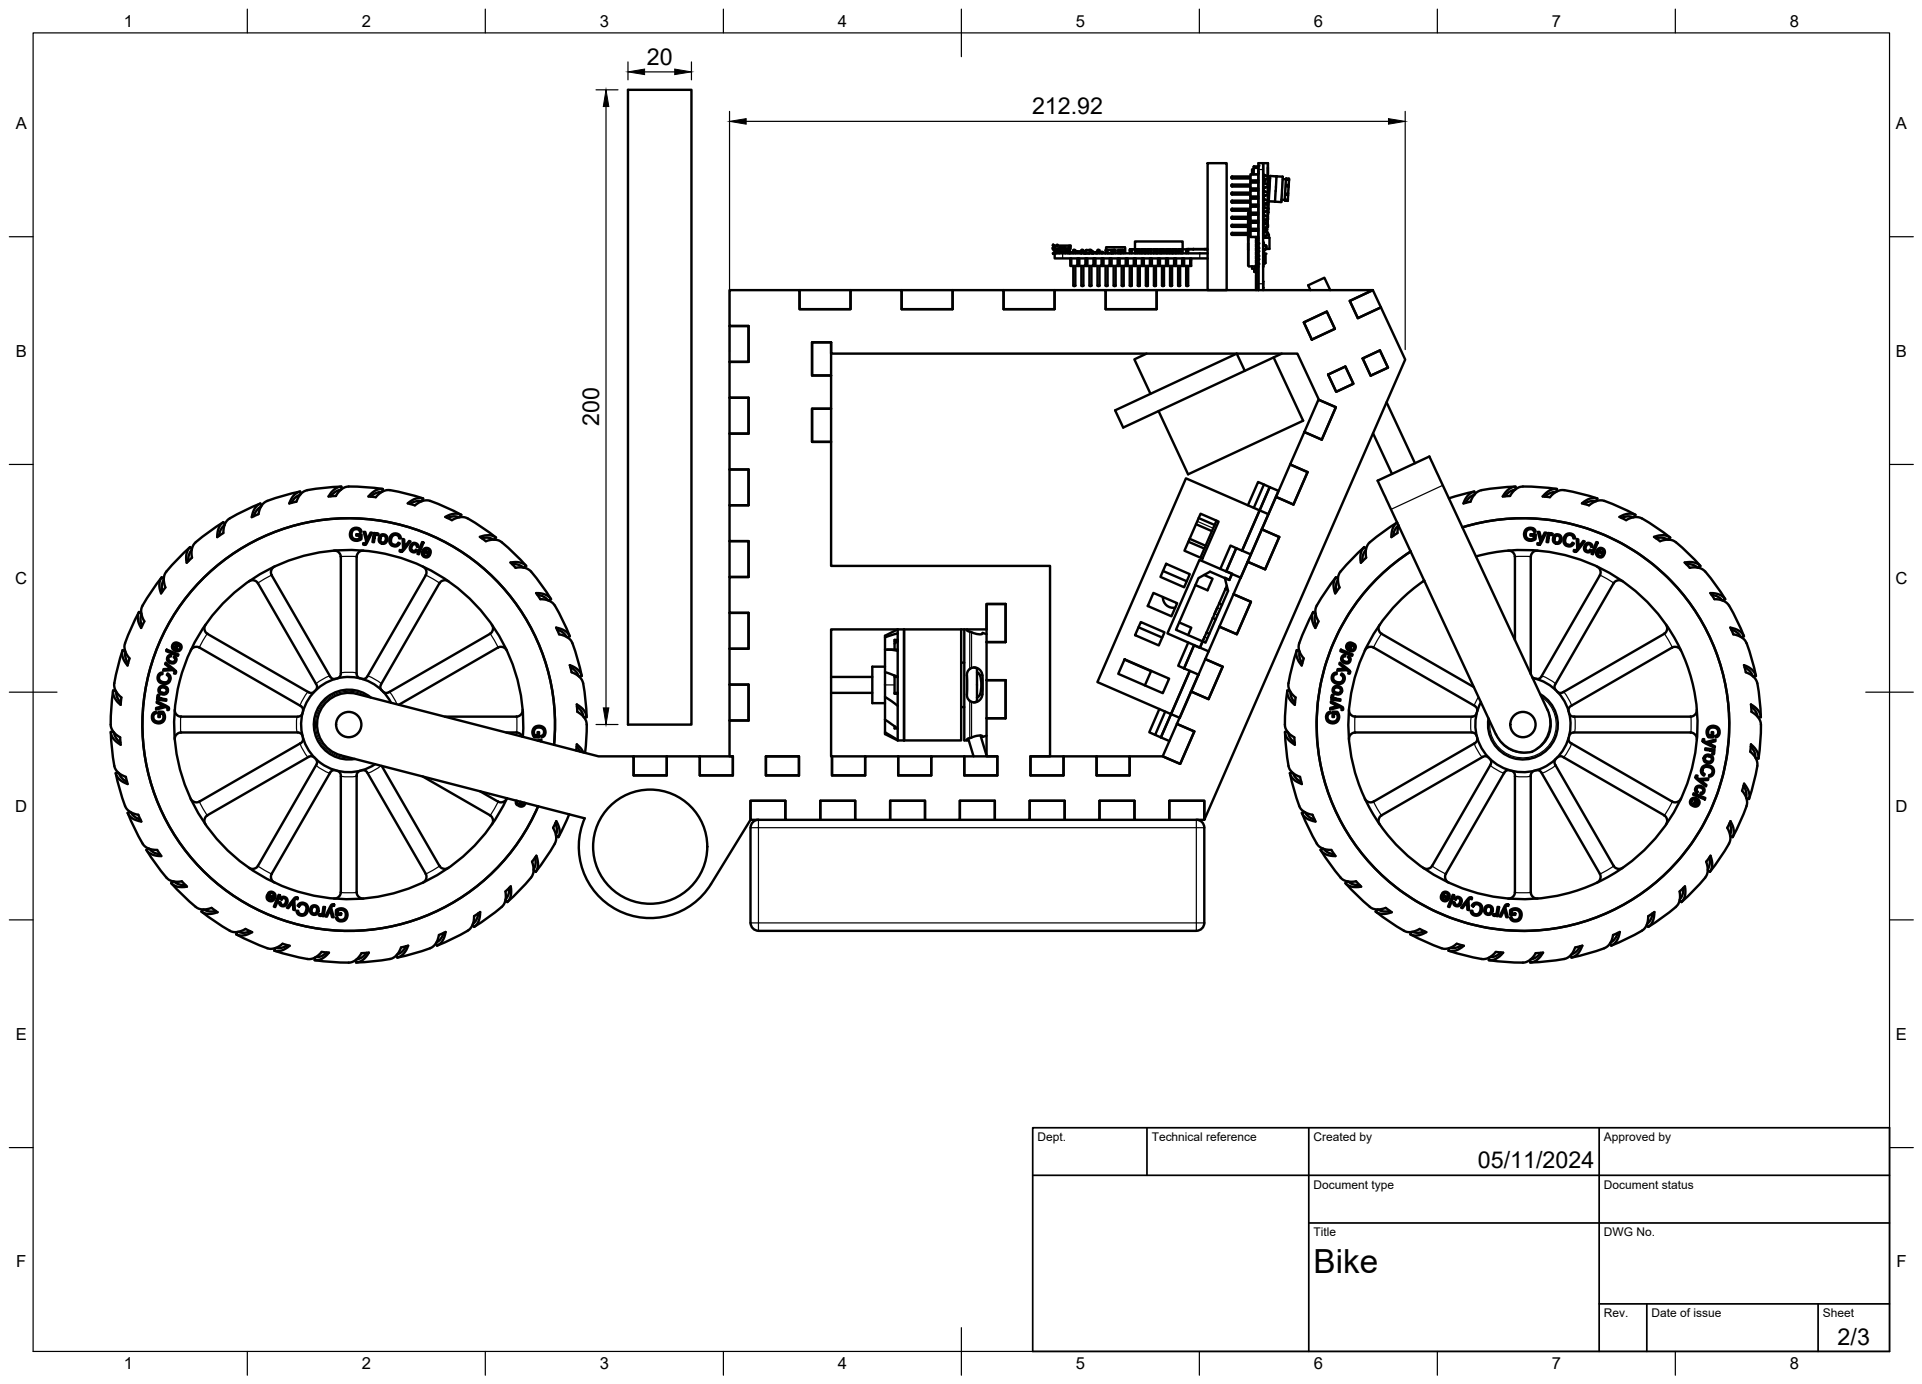
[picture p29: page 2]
Title; DWG No.

Dept. | Technical reference | Created by 05/11/2024 | Approved by

Document type | Document status

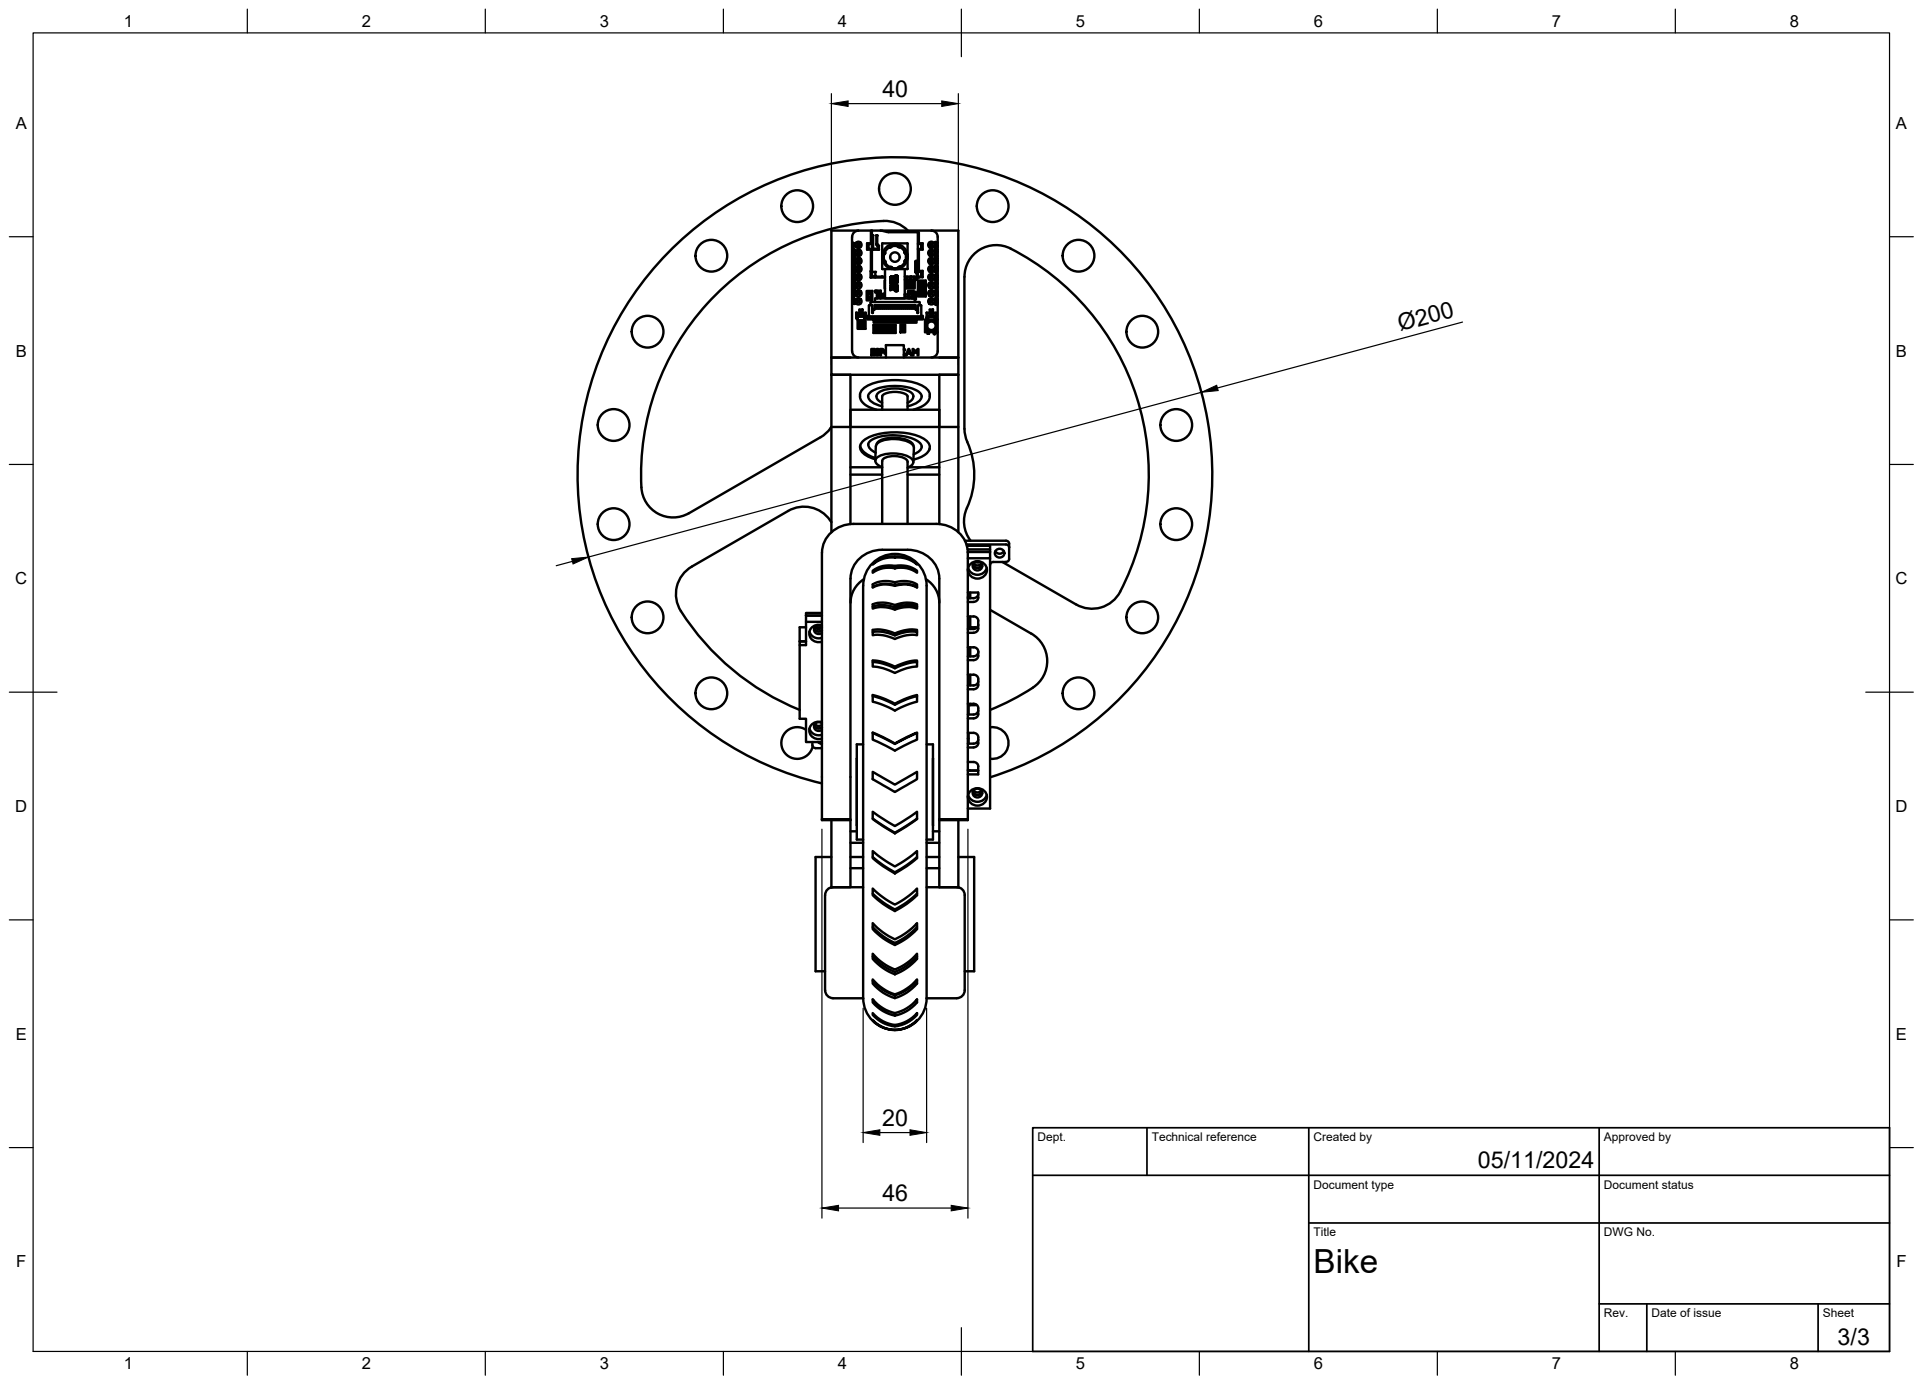
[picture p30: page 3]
Title; DWG No.

Dept. | Technical reference | Created by 05/11/2024 | Approved by

Document type | Document status

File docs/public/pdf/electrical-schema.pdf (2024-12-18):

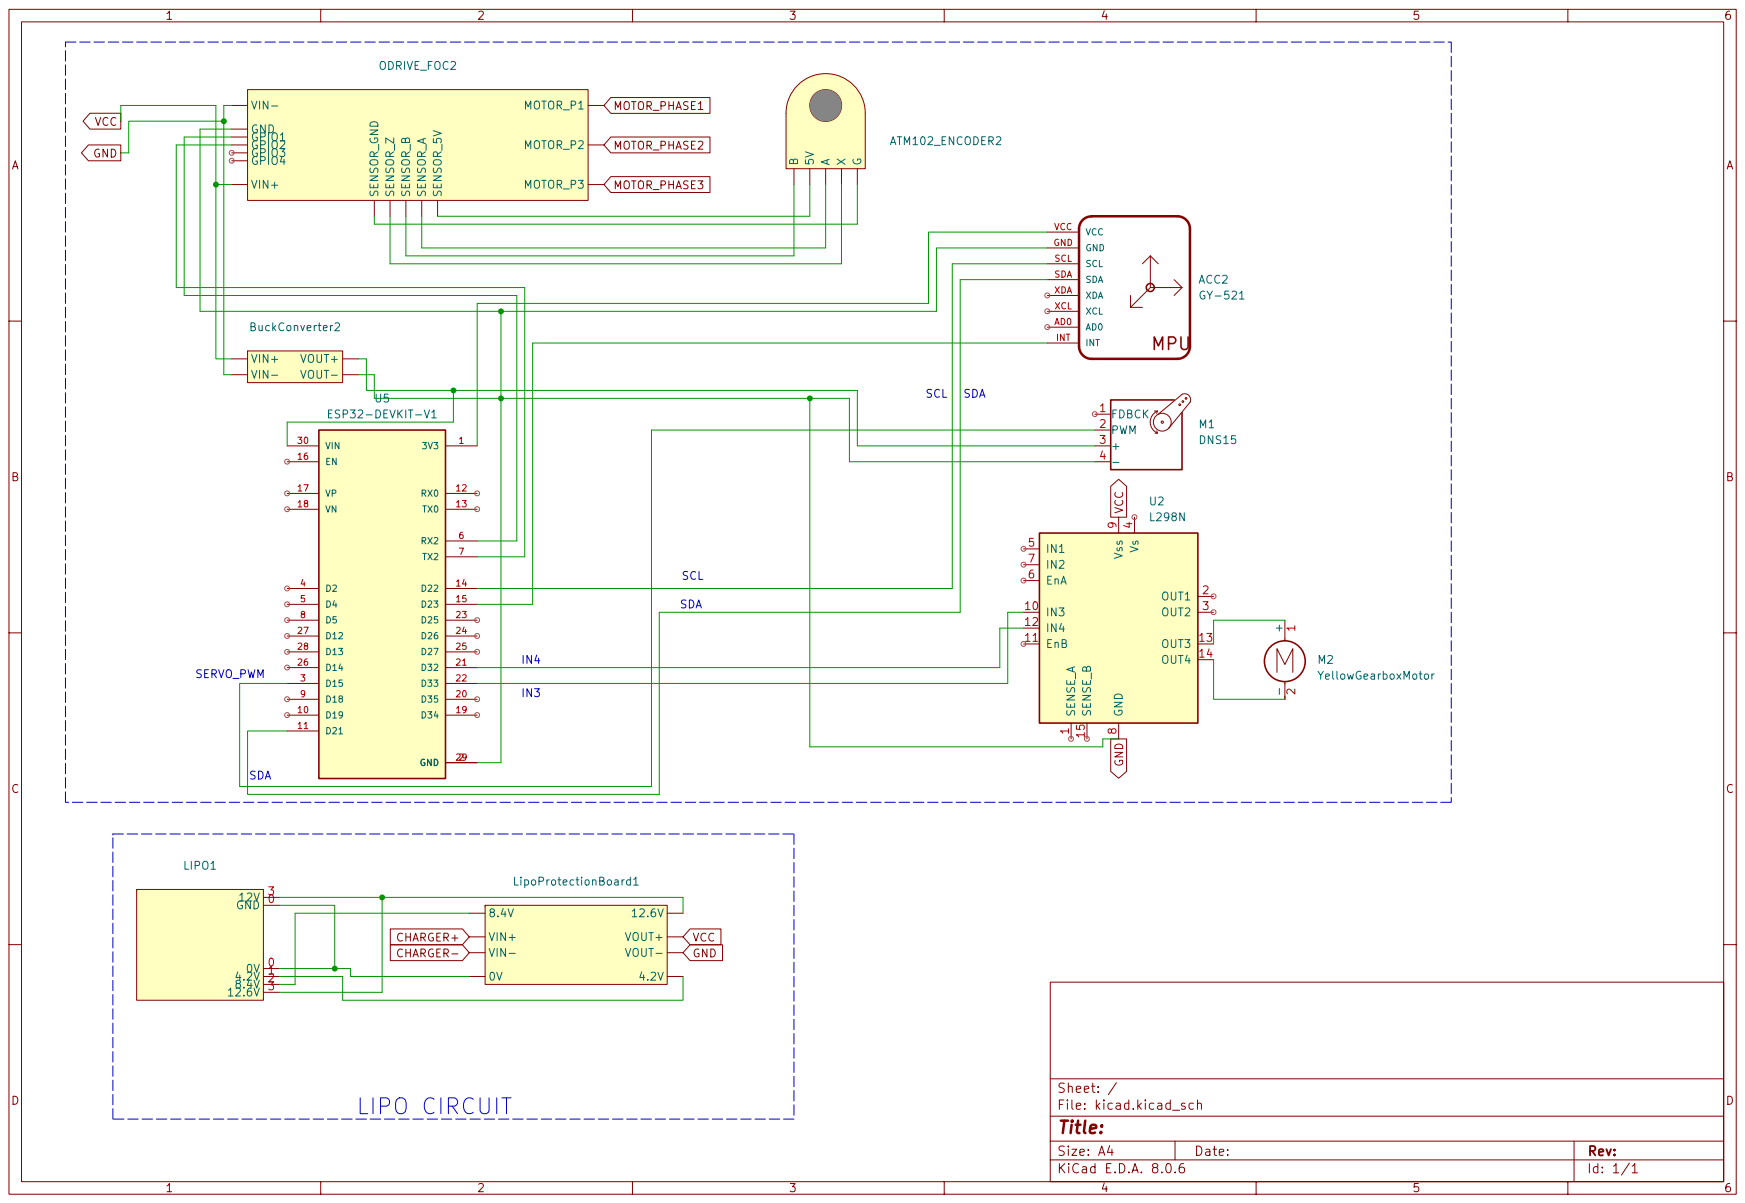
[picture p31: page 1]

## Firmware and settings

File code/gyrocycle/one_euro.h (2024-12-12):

/* -*- coding: utf-8 -*-
 *
 * 1euroFilter.h -
 *
 * Authors:
 * Nicolas Roussel (nicolas.roussel@inria.fr)
 * Géry Casiez https://gery.casiez.net
 *
 * Copyright 2019 Inria
 *
 * BSD License https://opensource.org/licenses/BSD-3-Clause
 *
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
 * 3. Neither the name of the copyright holder nor the names of its contributors may be used to endorse or
 * promote products derived from this software without specific prior written permission.

 * THIS SOFTWARE IS PROVIDED BY THE COPYRIGHT HOLDERS AND CONTRIBUTORS "AS IS" AND ANY EXPRESS OR IMPLIED WARRANTIES,
 * INCLUDING, BUT NOT LIMITED TO, THE IMPLIED WARRANTIES OF MERCHANTABILITY AND FITNESS FOR A PARTICULAR PURPOSE ARE
 * DISCLAIMED. IN NO EVENT SHALL THE COPYRIGHT HOLDER OR CONTRIBUTORS BE LIABLE FOR ANY DIRECT, INDIRECT, INCIDENTAL,
 * SPECIAL, EXEMPLARY, OR CONSEQUENTIAL DAMAGES (INCLUDING, BUT NOT LIMITED TO, PROCUREMENT OF SUBSTITUTE GOODS OR SERVICES;
 * LOSS OF USE, DATA, OR PROFITS; OR BUSINESS INTERRUPTION) HOWEVER CAUSED AND ON ANY THEORY OF LIABILITY, WHETHER IN
 * CONTRACT, STRICT LIABILITY, OR TORT (INCLUDING NEGLIGENCE OR OTHERWISE) ARISING IN ANY WAY OUT OF THE USE OF THIS
 * SOFTWARE, EVEN IF ADVISED OF THE POSSIBILITY OF SUCH DAMAGE.
 *
 */

#if (ARDUINO >= 100)
#include <Arduino.h>
#else
#include <WProgram.h>
#endif

#include <inttypes.h>

#ifndef ONEEUROFILTER
#define ONEEUROFILTER

// -----------------------------------------------------------------
// Utilities

typedef float TimeStamp; // in seconds

static const TimeStamp UndefinedTime = -1.0;

// -----------------------------------------------------------------

#define DEFAULT_FREQUENCY 120 // [Hz] default frequency of your incoming noisy data
#define DEFAULT_MINCUTOFF 1.0 // [Hz] needs to be tuned
#define DEFAULT_BETA 0        // Needs to be tuned
#define DEFAULT_DCUTOFF 1.0   // [Hz] should not be changed

class LowPassFilter
{

    float y, a, s;
    bool initialized;

    void setAlpha(float alpha);

public:
    LowPassFilter(float alpha, float initval = 0.0);

    float filter(float value);

    float filterWithAlpha(float value, float alpha);

    bool hasLastRawValue(void);

    float lastRawValue(void);

    float lastFilteredValue(void);
};

// -----------------------------------------------------------------

class OneEuroFilter
{

    float freq;
    float mincutoff;
    float beta_;
    float dcutoff;
    LowPassFilter *x;
    LowPassFilter *dx;
    TimeStamp lasttime;

    // implicitly implemented, not to be used
    OneEuroFilter(const OneEuroFilter &);
    OneEuroFilter &operator=(const OneEuroFilter &);

    float alpha(float cutoff);

    void setDerivateCutoff(float dc);

public:
    explicit OneEuroFilter(float freq = DEFAULT_FREQUENCY,
                           float mincutoff = DEFAULT_MINCUTOFF, float beta_ = DEFAULT_BETA, float dcutoff = DEFAULT_DCUTOFF);

    /**
     * @brief Creates the filter and set its parameters
     * @param freq An estimate of the frequency in Hz of the signal (> 0), if timestamps are not available.
     * @param mincutoff Min cutoff frequency in Hz (> 0). Lower values allow to remove more jitter.
     * @param beta_ Parameter to reduce latency (> 0).
     * @param dcutoff Used to filter the derivates. 1 Hz by default. Change this parameter if you know what you are doing.
     */
    void begin(float freq,
               float mincutoff = 1.0, float beta_ = 0.0, float dcutoff = 1.0);

    /**
     * @brief Sets the frequency of the signal
     * @param f An estimate of the frequency in Hz of the signal (> 0), if timestamps are not available.
     */
    void setFrequency(float f);

    /**
     * @brief Sets the filter min cutoff frequency
     * @param mc Min cutoff frequency in Hz (> 0). Lower values allow to remove more jitter.
     */
    void setMinCutoff(float mc);

    /**
     * @brief Sets the Beta parameter
     * @param b Parameter to reduce latency (> 0).
     */
    void setBeta(float b);

    /**
     * @brief Filter the noisy signal
     * @param value Noisy value to filter
     * @param timestamp (optional) timestamp in seconds
     * @return The filtered value
     */
    float filter(float value, TimeStamp timestamp = UndefinedTime);

    ~OneEuroFilter(void);
};

#endif

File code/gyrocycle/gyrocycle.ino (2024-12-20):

#include <Adafruit_MPU6050.h>
#include <Adafruit_Sensor.h>
#include <Wire.h>
#include <math.h>
#include "one_euro.h"

#define GEAR_RATIO 0.5
#define INITIAL_KALMAN_ANGLE -0.1
// 0.06981 corresponds to 4 deg of uncertainty on the first step
#define INITIAL_KALMAN_UNCERTAINTY 0.06981
#define TORQUE_FOR_CONSTANT_SPEED 0.018

// This defines how much the angle is influenced by the accelerometer and the gyroscope
#define ANGLE_ALPHA 0.1f
#define NUMBER_OF_MEASURE_FOR_MPU_CALIBRATION 500
#define MOVING_AVERAGE_SIZE 100

#define MINIMUM_VOLTAGE 11.3f // Volts

#define LEFT_STEERING_ANGLE 86
#define RIGHT_STEERING_ANGLE 94
#define DEFAULT_STEERING_ANGLE 90

#define MAX_TOTAL_ERROR 1

// Angle and uncertainty at each step
float angle = INITIAL_KALMAN_ANGLE;
float uncertainty = INITIAL_KALMAN_UNCERTAINTY;
unsigned long lastAngleUpdateTime = 0;
unsigned long currentTime = 0;

unsigned long lastLoopTime = 0;
unsigned long currentLoopTime = 0;

// model characteristics
const float mass = 2;               // in kg
const float centerOfGravity = 0.15; // in meters

// basic balancing constants
const float positionWeight = 1.2;
const float rotationWeight = 0.1;

// Which controller to use to determine what torque the flywheel should have
String controllerMode = "PID";

// Which filter to use for angle calculation
String filter = "KALMAN";

// Error terms for the PID controller
float previous_error = 0.0;
float total_error = 0.0;

// used to change the stabilization point
float angleCorrection = -0.01;

// margin of error for the angle to be considered vertical
float angleMargin = 0.00;

float setpointDelta = 0.02;
float setpoint = 0;

// PID constants
float Kp = 1.5;
float Ki = 0.0000001;
float Kd = 0.1;

// Indicates whether the current running mode is configuration or balancing
int isInConfigurationMode = 1;

// Indicates whether to print values for plotting when balancing or not
bool plotterEnabled = true;

OneEuroFilter oneEuroGyroFilter = OneEuroFilter(DEFAULT_FREQUENCY, 1.0, 0.01, DEFAULT_DCUTOFF);
OneEuroFilter oneEuroAngleAccFilter = OneEuroFilter(DEFAULT_FREQUENCY, 1.0, 0.01, DEFAULT_DCUTOFF);

float movingAverage[MOVING_AVERAGE_SIZE];
int movingAverageIndex = 0;

void switchMode()
{
  isInConfigurationMode = !isInConfigurationMode;

  // Once the state is updated, do some transition logic
  if (isInConfigurationMode)
  {
    Serial.println("Exiting balancing mode, stopping motor...");
    stopFlywheelMotor();
    Serial.println("Motor stopped.");
    Serial.println("Entering configuration mode. Type 'help' for a list of available commands.");
  }
  else
  {
    Serial.println("Preparing for balancing mode...");
    Serial.println("Resetting state variables...");
    angle = INITIAL_KALMAN_ANGLE;
    uncertainty = INITIAL_KALMAN_UNCERTAINTY;
    lastAngleUpdateTime = 0;
    currentTime = 0;
    lastLoopTime = 0;
    currentLoopTime = 0;
    total_error = 0.0;
    Serial.println("State variables reset.");
    Serial.println("Entering balancing mode.");
  }
}

void calibrateInitialAngle(void)
{
  float sum = 0;
  for (int i = 0; i < NUMBER_OF_MEASURE_FOR_MPU_CALIBRATION; i++)
  {
    float accelY, accelZ, gyroX;
    mpuMeasure(&accelY, &accelZ, &gyroX);
    sum += atan(accelY / accelZ);
  }
  angle = sum / NUMBER_OF_MEASURE_FOR_MPU_CALIBRATION;
}

void setup(void)
{

  // Start the Serial communication
  Serial.begin(500000);

  // Wait for the Serial to be opened
  while (!Serial)
    delay(10);

  delay(2000);

  // Start I2C communication with the MPU6050 gyroscope sensor
  initMpuCommunication();

  Wire.setClock(400000);
  unsigned long clock = Wire.getClock();
  Serial.print("clock:");
  Serial.println(clock);

  // Start UART communication with ODrive motor controller
  initOdriveCommunication();

  Serial.println("Calibrating MPU6050...");
  calibrateInitialAngle();
  Serial.println("MPU6050 calibrated.");

  Serial.println("Setting up RemoteXY...");
  initMotion();
  Serial.println("RemoteXY ready");

  Serial.println("Setup complete.");
  Serial.print("Starting in 3...");
  delay(1000);
  Serial.print("2...");
  delay(1000);
  Serial.println("1...");
  delay(1000);
}

void loop()
{
  if (getVbusVoltage() < MINIMUM_VOLTAGE)
  {
    Serial.println("MINIMUM VOLTAGE ERROR");
    safetyStop();
    return;
  }

  handleRemoteControlEvents();
  updateGyroAngle();

  // Run one iteration at a time instead of blocking in configuration or balancing mode.
  // This allows RemoteXY to handle bluetooth inputs under the hood, between two loops.
  if (isInConfigurationMode)
  {
    // In configuration mode, the user can enter commands to calibrate and monitor the system.
    configurationMode();
  }
  else
  {
    // In balancing mode, the system tries to balance the bicycle.
    balancingMode();
  }
}

/**
 * Runs one iteration of the configuration mode. Because of how RemoteXY works, this function
 * has been designed not to block the execution of the loop.
 *
 * Hence, this function should be called inside a loop to keep the configuration mode running.
 *
 * Some commands (such as the ODrive REPL) are blocking, meaning they will not return until
 * they terminate completely.
 */
void configurationMode()
{
  if (Serial.available() > 0)
  {
    String command = Serial.readStringUntil('\n');
    if (command.startsWith("algo "))
    {
      String parts = command.substring(5);
      if (parts == "PID" || parts == "OG")
      {
        controllerMode = parts;
        Serial.print("Controller mode set to: ");
        Serial.println(controllerMode);
      }
      else
      {
        Serial.print("Unknown controller mode: '");
        Serial.print(parts);
        Serial.println("'.");
      }
    }
    else if (command == "calibrate_mpu")
    {
      calibrateMpu();
    }
    else if (command == "clear_errors")
    {
      Serial.println("Clearing errors...");
      Serial.println("Please note that depending on which ODrive you use, clearing errors might not be");
      Serial.println("a supported command. In that case, you'll have to restart your ODrive.");
      clearFlywheelErrors();
      Serial.println("Errors cleared (hopefully).");
    }
    else if (command == "config")
    {
      Serial.println("Usage: config <Kp> <Ki> <Kd> <max_fw_torque> <odrive_max_speed> <setpoint_delta> <angle_correction>, <angle_margin>");
    }
    else if (command.startsWith("config "))
    {
      // Extract the values from the command
      String parts = command.substring(7);
      float newKp, newKi, newKd, max_fw_torque, odrive_max_speed, newSetpoint, newAngleCorrection, newAngleMargin;
      sscanf(parts.c_str(), "%f %f %f %f %f %f %f %f", &newKp, &newKi, &newKd, &max_fw_torque, &odrive_max_speed, &newSetpoint, &newAngleCorrection, &newAngleMargin);

      // Update the values
      Kp = newKp;
      Ki = newKi;
      Kd = newKd;
      setFlywheelMaxTorque(max_fw_torque);
      setOdriveConfigMaxSpeed(odrive_max_speed);
      setpointDelta = newSetpoint;
      angleCorrection = newAngleCorrection;
      angleMargin = newAngleMargin;

      // Notify the user of the update
      Serial.print("New configuration: Kp=");
      Serial.print(Kp);
      Serial.print(", Ki=");
      Serial.print(Ki);
      Serial.print(", Kd=");
      Serial.print(Kd);
      Serial.print(", max_fw_torque=");
      Serial.print(max_fw_torque);
      Serial.print(", odrive_max_speed=");
      Serial.print(odrive_max_speed);
      Serial.print(", setpoint_delta=");
      Serial.print(setpointDelta);
      Serial.print(", angle_correction=");
      Serial.print(angleCorrection);
      Serial.print(", angle_margin=");
      Serial.println(angleMargin);
    }
    else if (command == "debug")
    {
      printMaxReached();
    }
    else if (command.startsWith("filter ")) {
      String parts = command.substring(7);
      if (parts == "KALMAN" || parts == "EURO")
      {
        filter = parts;
        Serial.print("Filter set to: ");
        Serial.println(filter);
      }
      else
      {
        Serial.print("Unknown filter: '");
        Serial.print(parts);
        Serial.println("'.");
      }
    }
    else if (command == "help")
    {
      Serial.println("===========================================");
      Serial.println();
      Serial.println("AVAILABLE COMMANDS");
      Serial.println();
      Serial.println("===========================================");
      Serial.println();
      Serial.println("---------------- algo [PID/OG]");
      Serial.println("Sets the controller mode to PID or original (OG).");
      Serial.println();
      Serial.println("---------------- calibrate_mpu");
      Serial.println("Enters calibration mode for the MPU6050 to set the offsets.");
      Serial.println();
      Serial.println("---------------- clear_errors");
      Serial.println("Clears the errors of the ODrive driver so that the motor can keep going.");
      Serial.println("Note that some ODrive versions do not support clearing their errors as a command and");
      Serial.println("require to be restarted in order to reset their error state.");
      Serial.println();
      Serial.println("---------------- config <Kp> <Ki> <Kd> <max_fw_torque> <odrive_max_speed> <setpoint_delta> <angle_correction> <angle_margin>");
      Serial.println("Sets all configuration parameters. Used to easily save and reproduce a configuration across runs.");
      Serial.println();
      Serial.println("---------------- debug");
      Serial.println("Prints reached maxima in prior testing and resets detectors");
      Serial.println();
      Serial.println("---------------- filter <EURO/KALMAN>");
      Serial.println("Sets the filter used to reduce noise in the angle measurement. The default value on startup is KALMAN");
      Serial.println();
      Serial.println("---------------- help");
      Serial.println("Displays a list of the existing commands.");
      Serial.println();
      Serial.println("---------------- plotter <on/off/true/false/1/0>");
      Serial.println("Enables/disables plotting logs (if enabled, the MCU will send Serial debug data).");
      Serial.println();
      Serial.println("---------------- print");
      Serial.println("Prints the current configuration with all necessary values to write them down somewhere.");
      Serial.println();
      Serial.println("---------------- odrive_repl");
      Serial.println("Starts a REPL session with the ODrive where you can enter commands for the ODrive directly.");
      Serial.println();
      Serial.println("---------------- set [Kp/Ki/Kd/max_fw_torque/odrive_max_speed/setpoint_delta/angle_correction/angle_margin] <value>");
      Serial.println("Sets the named value (Kp, Ki, Kd, max_fw_torque, odrive_max_speed, setpoint_delta, angle_correction, angle_margin) to the provided value.");
      Serial.println();
      Serial.println("---------------- start");
      Serial.println("Exits the configuration mode and starts the balancing loop.");
      Serial.println();
      Serial.println("===========================================");
    }
    else if (command.startsWith("plotter"))
    {
      if (command == "plotter on" || command == "plotter true" || command == "plotter 1")
      {
        plotterEnabled = true;
        Serial.println("Plotting logs are now enabled.");
      }
      else if (command == "plotter off" || command == "plotter false" || command == "plotter 0")
      {
        plotterEnabled = false;
        Serial.println("Plotting logs are now disabled.");
      }
      else
      {
        Serial.println("Usage: plotter <on/off/true/false/1/0>");
      }
    }
    else if (command == "print")
    {
      Serial.println("===========================================");
      Serial.println();
      Serial.println("CURRENT CONFIGURATION");
      Serial.println();
      Serial.println("===========================================");
      Serial.println("ODrive:");
      printOdriveConfiguration();
      Serial.println("===========================================");
      Serial.println("MPU6050:");
      printMpuConfiguration();
      Serial.println("===========================================");
      Serial.println("PID and algorithm:");
      Serial.print("Kp: ");
      Serial.println(Kp);
      Serial.print("Ki: ");
      Serial.println(Ki);
      Serial.print("Kd: ");
      Serial.println(Kd);
      Serial.print("");
      Serial.print("Algorithm: ");
      Serial.println(controllerMode);
      Serial.print("Filter: ");
      Serial.println(filter);
      Serial.print("Set point: ");
      Serial.println(setpointDelta);
      Serial.print("Angle correction: ");
      Serial.println(angleCorrection);
      Serial.println("===========================================");
      Serial.println("General:");
      Serial.print("Plotting enabled: ");
      Serial.println(plotterEnabled);
      Serial.println("===========================================");
    }
    else if (command == "odrive_repl")
    {
      odriveRepl();
    }
    else if (command.startsWith("set "))
    {
      String name = command.substring(4);
      float value = name.substring(name.indexOf(' ') + 1).toFloat();
      if (name.startsWith("Kp "))
      {
        Kp = value;
        Serial.print("New Kp: ");
        Serial.println(Kp);
      }
      else if (name.startsWith("Ki "))
      {
        Ki = value;
        Serial.print("New Ki: ");
        Serial.println(Ki);
      }
      else if (name.startsWith("Kd "))
      {
        Kd = value;
        Serial.print("New Kd: ");
        Serial.println(Kd);
      }
      else if (name.startsWith("max_fw_torque "))
      {
        setFlywheelMaxTorque(value);
        Serial.print("New max flywheel torque: ");
        Serial.println(value);
      }
      else if (name.startsWith("odrive_max_speed "))
      {
        setOdriveConfigMaxSpeed(value);
        Serial.print("New ODrive max speed: ");
        Serial.println(value);
      }
      else if (name.startsWith("setpoint_delta ")) {
        setpointDelta = value;
        Serial.print("New setpoint delta: ");
        Serial.println(value);
      }
      else if (name.startsWith("angle_correction ")) {
        angleCorrection = value;
        Serial.print("New angle correction: ");
        Serial.println(value);
      }
      else if (name.startsWith("angle_margin ")) {
        angleMargin = value;
        Serial.print("New angle margin: ");
        Serial.println(value);
      }
      else
      {
        Serial.print("Unknown constant: '");
        Serial.print(name);
        Serial.println("'.");
      }
    }
    else if (command == "start")
    {
      switchMode();
    }
    else
    {
      Serial.print("Unknown command: '");
      Serial.print(command);
      Serial.println("'.");
    }
  }
}

void updateGyroAngle()
{
  float accelY, accelZ, gyroX, gyroY, gyroZ;
  mpuMeasure(nullptr, &accelY, &accelZ, &gyroX, &gyroY, &gyroZ);

  if (filter == "KALMAN")
  {
    angleCalculatorKalman(accelY, accelZ, gyroX);
  }
  else if (filter == "EURO")
  {
    angleCalculatorEuro(accelY, accelZ, gyroX, gyroY, gyroZ);
  }
}

void balancingMode()
{
  // Check that the angle is within the safety bounds, otherwise stop balancing
  if (angle <= (-M_PI / 4) || angle >= (M_PI / 4))
  {
    Serial.println("Safety angle limit reached, stopping motor...");
    switchMode();
    return;
  }

  // Check that the user did not stop the balancing mode manually
  if (Serial.available() > 0)
  {
    Serial.readStringUntil('\n');
    switchMode();
    requestSteeringAngle(DEFAULT_STEERING_ANGLE);
    return;
  }

  currentLoopTime = micros();

  // flywheel motor input (constrained for safety)
  float input = 0;
  if (controllerMode == "PID")
  {
    if (angle > setpointDelta/2.0f) {
      setpoint = -setpointDelta;
    } else if (angle < -setpointDelta/2.0f) {
      setpoint = setpointDelta;
    }
    input = pidBalancingImplementation(currentLoopTime - lastLoopTime, angle, 0);
  }

  if (input < -0.03)
  {
    requestSteeringAngle(LEFT_STEERING_ANGLE);
  }
  else if (input > 0.03)
  {
    requestSteeringAngle(RIGHT_STEERING_ANGLE);
  }
  else
  {
    requestSteeringAngle(DEFAULT_STEERING_ANGLE);
  }

  // monitoring purposes
  if (plotterEnabled)
  {
    Serial.print("elapsedTime(microseconds):");
    Serial.print(currentLoopTime - lastLoopTime);
    Serial.print(",");
    Serial.print("angle:");
    Serial.print(angle, 5);
    Serial.print(",");
    Serial.print("input:");
    Serial.print(input, 5);
    Serial.print(",");
    Serial.print("velocity:");
    Serial.println(getFlywheelMotorSpeed());
  }

  setFlywheelMotorTorque(input);

  lastLoopTime = currentLoopTime;
}

/**
 * @brief Original implementation of balancing.
 *
 * Performs some computations based on the current angle of the bike, and predicts
 * the torque that should be applied to the flywheel motor.
 *
 * @param angle The angle from the vertical, calculated with the accelerometer.
 * @return float The torque that should be applied to the flywheel motor.
 */
float ogBalancingImplementation(float gyroX, float angle)
{
  // Calculate the theoretical torque that should be applied to the flywheel motor
  float theoreticalTorque = centerOfGravity * mass * 9.81 * sin(angle) * GEAR_RATIO;

  // Calculate the input to the flywheel motor
  float input = positionWeight * theoreticalTorque + rotationWeight * gyroX;

  return input;
}

/**
 * @brief Implementation of balancing algorithm using a PID controller.
 *
 * @param elapsedTime The time elapsed since the last iteration of the PID controller.
 * @param angle The angle from the vertical, calculated with the accelerometer.
 * @param setpoint The setpoint we want to go to
 *
 * @return float The torque that should be applied to the flywheel motor.
 */
float pidBalancingImplementation(unsigned long elapsedTime, float angle, float setpoint)
{
  // The error of this controller is the angle from the vertical
  float error = angle - angleCorrection - setpoint;
  if (-angleMargin < error && error < angleMargin)
  {
    error = 0;
    return 0;
  }
  // if (angle < 0) error = -error;

  // Accumulate the error for the integral (I) term
  // TODO : Should we clamp the value of total_error?
  total_error += error * elapsedTime / 1000000.0;
  if (total_error > MAX_TOTAL_ERROR)
  {
    total_error = MAX_TOTAL_ERROR;
  }
  else if (total_error < -MAX_TOTAL_ERROR)
  {
    total_error = -MAX_TOTAL_ERROR;
  }

  // Calculate the derivative (D) term
  float derivative = (error - previous_error) / (elapsedTime / 1000000.0);

  // Update the previous error
  previous_error = error;

  // Calculate the input to the flywheel motor
  return Kp * error + Ki * total_error + Kd * derivative;
}

// calculates tilt angle from sensor readings
void angleCalculatorKalman(float accelY, float accelZ, float gyroX)
{
  unsigned long currentTime = micros();

  float acc_angle = atan(accelY / accelZ);                                            // angle calculated with accelerometer readings
  float gyro_angle = angle + (currentTime - lastAngleUpdateTime) / 1000000.0 * gyroX; // angle integrated from gyroscope readings

  float uncertainty = uncertainty + ((currentTime - lastAngleUpdateTime) / 1000000.0) * ((currentTime - lastAngleUpdateTime) / 1000000.0) * 0.00487; // 0,00487 is the assumed variance on the rotation rate (std deviation of 4 deg/s)
  // calculate kalman gain
  float gain = uncertainty / (uncertainty + 0.00274); // 0.00274 is the assumed variance of the measured angle with the accelerometer (std deviation of 3 deg)
  // angle calculated with the kalman filter
  angle = gyro_angle + gain * (acc_angle - gyro_angle);
  // update uncertainty
  uncertainty = (1 - gain) * uncertainty;

  lastAngleUpdateTime = currentTime;
}

void angleCalculatorEuro(float accelY, float accelZ, float gyroX, float gyroY, float gyroZ)
{
  unsigned long currentTime = micros();
  float filteredGyroX = oneEuroGyroFilter.filter(gyroX, (float)(currentTime / 1000000.0f));
  float predictedAngle = angle + (float)(currentTime - lastAngleUpdateTime) / 1000000.0f * filteredGyroX;
  float filteredAccAngle = oneEuroAngleAccFilter.filter((float)atan(accelY / accelZ), (float)(currentTime / 1000000.0f));

  // This correct term is the angle calculated with the accelerometer
  float newAngle = 0.0;

  // If the gyroscope is not moving, the accelerometer is more reliable
  if (filteredGyroX < 0.01f && filteredGyroX > -0.01f && gyroY < 0.1f && gyroY > -0.1f && gyroZ < 0.1f && gyroZ > -0.1f)
  {
    newAngle = (float)((1 - ANGLE_ALPHA) * predictedAngle + ANGLE_ALPHA * filteredAccAngle);
  }
  else
  {
    newAngle = (float)(ANGLE_ALPHA * predictedAngle + (1 - ANGLE_ALPHA) * filteredAccAngle);
  }
  angle = newAngle;
  lastAngleUpdateTime = currentTime;
}

void stopAll()
{
  stopFlywheelMotor();
  stopPropulsionMotor();
}

void safetyStop()
{
  Serial.println("SAFETY STOP TRIGGERED");
  while (1)
  {
    stopFlywheelMotor();
    stopPropulsionMotor();
  }
}

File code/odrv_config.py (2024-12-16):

#!/usr/bin/env python3

import odrive
from odrive.enums import *
from odrive.enums import MOTOR_TYPE_HIGH_CURRENT, AXIS_STATE_MOTOR_CALIBRATION, AXIS_STATE_IDLE, \
    AXIS_STATE_ENCODER_OFFSET_CALIBRATION, CONTROL_MODE_TORQUE_CONTROL, INPUT_MODE_TORQUE_RAMP
import time

def wait_for_state(axis, requested_state, timeout=10):
    """Helper function to wait for axis to enter specified state"""
    start_time = time.time()
    while axis.current_state != requested_state:
        time.sleep(0.1)
        if time.time() - start_time > timeout:
            raise TimeoutError(f"Timeout waiting for state {requested_state}")

def reconnect_to_odrive():
    """Helper function to reconnect to ODrive after reboot"""
    print("Attempting to reconnect...")
    attempts = 0
    while attempts < 3:  # Try up to 3 times
        try:
            odrv0 = odrive.find_any()
            test = odrv0.vbus_voltage
            print(f"Reconnection successful. Bus voltage: {test}V")
            return odrv0
        except:
            print(f"Reconnection attempt {attempts + 1} failed, retrying...")
            time.sleep(2)
            attempts += 1
    
    raise Exception("Failed to reconnect to ODrive after multiple attempts")

def configure_odrive():
    print("Looking for ODrive...")
    
    try:
        odrv0 = odrive.find_any()
        print("Found ODrive")
    except:
        raise Exception("No ODrive found. Is it connected?")

    # Erase configuration
    try:
        odrv0.erase_configuration()
        print("ODrive is rebooting after erase...")
        time.sleep(5)
    except:
        print("Erase configuration failed - this is normal if connection was lost")
    
    odrv0 = reconnect_to_odrive()

    # Power configuration
    print("Configuring power parameters...")
    odrv0.config.brake_resistance = 2
    odrv0.config.dc_max_positive_current = 18
    odrv0.config.dc_bus_undervoltage_trip_level = 8.0
    odrv0.config.dc_bus_overvoltage_trip_level = 56.0
    odrv0.config.dc_max_negative_current = -3.0
    odrv0.config.max_regen_current = 0
    odrv0.save_configuration()

    print("Rebooting ODrive...")
    try:
        odrv0.reboot()
    except:
        print("Reboot command failed - this is normal")
    time.sleep(5)
    odrv0 = reconnect_to_odrive()

    # Motor configuration
    print("Configuring motor parameters...")
    odrv0.axis0.motor.config.pole_pairs = 7
    odrv0.axis0.motor.config.torque_constant = 8.27 / 1200
    odrv0.axis0.motor.config.current_lim = 35
    odrv0.axis0.motor.config.calibration_current = 15
    odrv0.axis0.motor.config.resistance_calib_max_voltage = 2
    odrv0.axis0.motor.config.motor_type = MOTOR_TYPE_HIGH_CURRENT
    odrv0.axis0.motor.config.requested_current_range = 35
    odrv0.axis0.encoder.config.cpr = 8192
    odrv0.axis0.config.calibration_lockin.current = 15
    odrv0.save_configuration()

    print("Rebooting ODrive...")
    try:
        odrv0.reboot()
    except:
        print("Reboot command failed - this is normal")
    time.sleep(5)
    odrv0 = reconnect_to_odrive()

    # Controller configuration
    print("Configuring controller parameters...")
    odrv0.axis0.controller.config.control_mode = CONTROL_MODE_TORQUE_CONTROL
    odrv0.axis0.controller.config.vel_limit = 50
    odrv0.axis0.controller.config.pos_gain = 30
    odrv0.axis0.controller.config.vel_gain = 0.008
    odrv0.axis0.controller.config.vel_integrator_gain = 0.05
    odrv0.axis0.controller.config.input_mode = INPUT_MODE_TORQUE_RAMP
    odrv0.axis0.controller.config.torque_ramp_rate = 100
    odrv0.save_configuration()
    
    print("Rebooting ODrive...")
    try:
        odrv0.reboot()
    except:
        print("Reboot command failed - this is normal")
    time.sleep(5)
    odrv0 = reconnect_to_odrive()

    # Motor calibration
    print("Starting motor calibration...")
    odrv0.axis0.requested_state = AXIS_STATE_MOTOR_CALIBRATION
    wait_for_state(odrv0.axis0, AXIS_STATE_IDLE)
    
    odrv0.axis0.motor.config.pre_calibrated = True
    odrv0.save_configuration()

    # Encoder calibration
    print("Starting encoder offset calibration...")
    odrv0.axis0.requested_state = AXIS_STATE_ENCODER_OFFSET_CALIBRATION
    wait_for_state(odrv0.axis0, AXIS_STATE_IDLE)

    # Startup configuration
    odrv0.axis0.config.startup_encoder_offset_calibration = True
    odrv0.axis0.config.startup_closed_loop_control = False
    odrv0.axis0.encoder.config.use_index = False
    odrv0.save_configuration()
    
    print("Rebooting ODrive...")
    try:
        odrv0.reboot()
    except:
        print("Reboot command failed - this is normal")
    time.sleep(5)
    odrv0 = reconnect_to_odrive()

    # Final configuration
    odrv0.axis0.config.startup_encoder_index_search = False
    odrv0.axis0.encoder.config.use_index = False
    odrv0.axis0.encoder.config.pre_calibrated = False
    odrv0.save_configuration()

    print("Rebooting ODrive...")
    try:
        odrv0.reboot()
    except:
        print("Reboot command failed - this is normal")
    time.sleep(5)
    odrv0 = reconnect_to_odrive()
    
    print("Setup complete!")
    return odrv0

if __name__ == "__main__":
    try:
        odrv = configure_odrive()
    except Exception as e:
        print(f"Setup failed with error: {str(e)}")

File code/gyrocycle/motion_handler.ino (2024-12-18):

//////////////////////////////////////////////
//        RemoteXY include library          //
//////////////////////////////////////////////

// Debug logging to Serial at 115200 can be enabled
//#define REMOTEXY_DEBUGLOG

// RemoteXY will select the connection mode and include necessary libraries
#define REMOTEXY_MODE__ESP32CORE_BLE

#include <BLEDevice.h>

// Setup RemoteXY connection settings
#define REMOTEXY_BLUETOOTH_NAME "RemoteXY"

#include <RemoteXY.h>
#include <ESP32Servo.h>

// RemoteXY GUI configuration that will be sent to the connecting device
#pragma pack(push, 1)  
uint8_t RemoteXY_CONF[] =   // 53 bytes
  { 255,3,0,0,0,46,0,19,0,0,0,0,31,1,200,84,1,1,3,0,
  4,177,4,16,77,48,2,26,4,3,32,77,16,176,2,26,2,89,4,26,
  14,0,2,26,31,31,79,78,0,79,70,70,0 };

// This structure defines all the variables and events of your control interface 
// 
struct {
    // input variables
  int8_t speedSlider; // from -100 to 100
  int8_t steeringSlider; // from -100 to 100
  uint8_t start_stop; // =1 if switch ON and =0 if OFF

    // other variable
  uint8_t connect_flag;  // =1 if wire connected, else =0

} RemoteXY;   
#pragma pack(pop)

/////////////////////////////////////////////
//           END RemoteXY include          //
/////////////////////////////////////////////

// The propulsion motor driver has two input pins IN1 and IN2 that must be
// wired to PWM pins on the microcontroller.
#define PROPULSION_PIN_1 32 // IN1
#define PROPULSION_PIN_2 33 // IN2
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

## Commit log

2024-11-04 docs: update the electrical schema
    [kicad.kicad_pcb, kicad.kicad_sch]
2024-11-05 docs: finish electrical schema
    [kicad.kicad_sch]
2024-11-05 docs: update proposal with cad drawings
2024-11-17 gyroscope related code
2024-11-18 Update gyrocycle.ino
    debugged code while testing with MPU6050
2024-11-21 Add bike body dxf files
    [bottom-plate.dxf, front-monting.dxf, left-side.dxf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]
2024-11-21 Add 3d files for fork and pulley
    [fork-shaft.stl, fork.stl]
2024-11-26 Update gyrocycle.ino
    Adapted code to work with an Arduino Uno and implemented balancing logic and communication with the odrive
2024-11-29 Update high view architecture with new MCU and motor
2024-12-03 refactor: move ODrive logic
2024-12-03 refactor: move gyroscope logic
2024-12-04 fix: adapt some constants
    First tests of the idle bicycle, we fixed a few constants for now.
    See #54
    [gyrocycle.ino, gyroscope_handler.ino, odrive_handler.ino]
2024-12-05 feat: implement interactive MPU calibration
2024-12-05 fix: String.split does not exist
    [gyroscope_handler.ino]
2024-12-05 feat: implement PID controller
2024-12-06 feat: add print and help commands
2024-12-06 feat: implement odrive repl
2024-12-06 Fix speed when out of bound torque
    [gyrocycle.ino]
2024-12-06 Fixed speed clamping, fixed controll mode selecting, added debug function to CLI
    [gyrocycle.ino, odrive_handler.ino]
2024-12-10 changed initial angle and added a non linear function to calculate error in pid
    [gyrocycle.ino]
2024-12-10 Edited electrical schema
    [kicad.kicad_sch]
2024-12-10 fix: wait for Odrive to be calibrated
    [odrive_handler.ino]
2024-12-10 docs: little fixes in CLI texts
    [gyrocycle.ino, odrive_handler.ino]
2024-12-11 feat: improve MPU calibration REPL
2024-12-11 fix: fix all-in-one command
    [gyrocycle.ino]
2024-12-11 feat: change gyroscope config
2024-12-11 changes due to testing gyro latency
2024-12-11 Change filter and tuning
2024-12-16 Update odrv_config.py
    Needed to wait for the odrive to reconnect
2024-12-16 Update motion_handler.ino
    Changed the pins for the propulsion motor.
2024-12-16 Update odrv_config.py
    Added some reboots. It works but it is possible that we can remove some of them.
    [odrv_config.py]
2024-12-16 Update gyrocycle.ino
    Added new default values
2024-12-16 Update odrive_handler.ino
    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
2024-12-16 Added voltage and fail safe defaults
    [gyrocycle.ino, motion_handler.ino, odrive_handler.ino]
2024-12-16 Fix steering and remove remoteXY waiting
    [gyrocycle.ino, motion_handler.ino]
2024-12-17 Move front wheel
2024-12-17 Update schematic
    [kicad.kicad_sch]
2024-12-17 Add front wheel support
2024-12-18 Update front wheel values and clamp total error
    [gyrocycle.ino]
2024-12-18 Update electrical schema
    [kicad.kicad_sch]
2024-12-18 docs: add documentation for GyroCycle
    * docs: setup documentation folder
    * docs: skeleton of the docs
    * docs: set up search feature for docs
    * docs: add "edit this page" link
    * fix: flatten logo, fix QR and glossary links
    * fix: improve bullet points indentation
    * docs: finish writing prerequisites
    * docs: soldering guide for MPU6050
    * docs: some additional notes about shaft
    * docs: other minor improvements
    * docs: implement STL viewer
    * docs: document shaft manufacturing
    * docs: zoom-in for the shaft image
    * docs: improve StlViewer component
    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
    [bicycle-mdf-bottom.dxf, bicycle-mdf-bottom.stl, bicycle-mdf-flywheel-holder.dxf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]
